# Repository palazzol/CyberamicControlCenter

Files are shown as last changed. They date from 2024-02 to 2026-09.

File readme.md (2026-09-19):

# Unofficial Cyberamic Control Center Archive #

This archive contains unofficial information about the Animatronics Control Computer designed the original Chuck E Cheese's Pizza Time Theatre.  The focus of this archive is to document the historical development and capabilities of this machine.

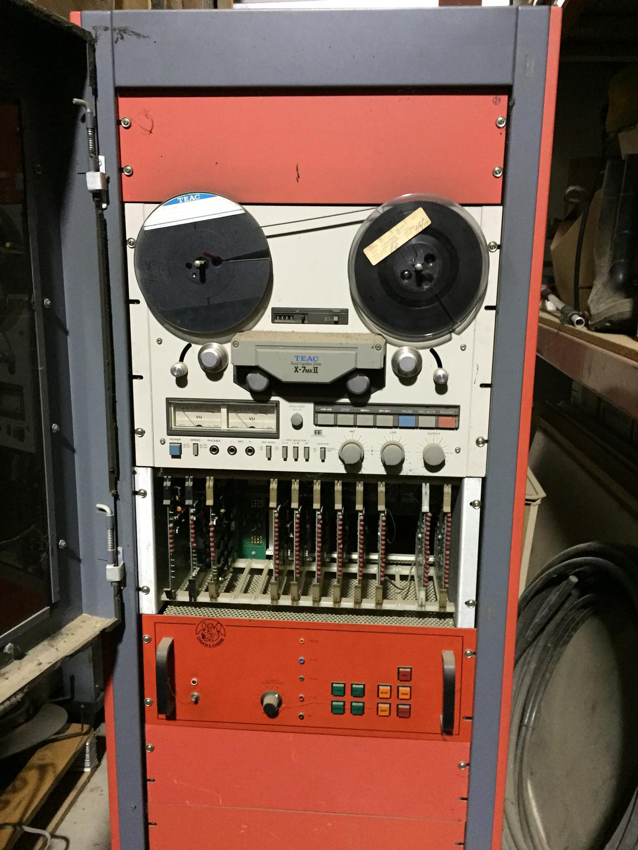
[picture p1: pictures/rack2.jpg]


It was reused in several incarnations over it's lifetime:

## Reel to Reel Configuration: ##
* Based on a 6502 processor and a TEAC Tape Deck, this computer controller the shows such as Dolli Dimples, The Beagles, The King, and the Balcony Stage.

## SVHS Configuration #1: ##
* This same hardware was adapted to play media from SVHS Media.

## SVHS Configuration #2: ##
* Upgraded with a M68HC11 processor, and an external media switcher, this continued to be used to play SVHS media.

## DVD Configuration: ##
* Adapted to DVD Media

If you have any more information or experience with this machine, and would like to help document it's history and behavior, please reach out!

# Latest protocol definitions as decoded from ROM images #
https://docs.google.com/spreadsheets/d/1zTHxSJqbsTTEe6A_9ltzb_rc91lcfIUvdmzVYEThIzg/edit?usp=sharing

# Questions: #

We're working on collecting as much information on how the original Pizza Time Theater system worked and have generated some questions:

* Did the original R2R system use 4-track audio at any stores?

Backplane:
* Was the original card cage a different size to accomodate the 0004 rev.a card?
* Why is the lights 50-pin connector recessed on the card compared to the character card?

Are there more board revisions beyond what we have? looking for:
* Audio board 0003 rev.a, rev.b, and beyond rev.c
* Audio board 0033 rev.b and beyond
* Character board 0004 rev.c and beyond
* Character board 0034 rev.b, rev.f and beyond
* Light board 0021 rev.b to rev.e
* Transport board 0020 rev.a
* Did the original transport card take a external uart clock? per the schematic
* Transport board 0020 rev.c
* CPU board 0001 rev.d and beyond 
* Random movements board?
* Board 0002?

Where are any other rom variants beyond what's in this archive?
* (We strongly believe the original balcony stage rom is not represented here)
* How do the other ROMs handle the buttons on the front panel?

Any more un-scanned documentation?
* Are there any more schematics? 
* Any documentation on how to hook up all the shows?

More show tapes on original media?
* More shows decoded?
* What are the formats for the decoding?
* Is there any metadata they missed like potentially more tracks?

Who else to talk to on this subject?

Extra parts we don't have?

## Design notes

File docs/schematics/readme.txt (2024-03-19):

These are partial, original schematics for the Cyberamic Control System.

The Backplane, Character, and Light Driver schematics seem to be accurate.
However, I do not have a J-19 on my Backplane, nor traces coming from those pins.

I do not have a Solenoid board, or a Transport board, but they seem to be reasonable from the pictures I've seen.

The Audio board schematic is still not found.  I think that board has been accurately replicated in KiCAD. (Evan A. March 19 2024)

The Audio board was the first board to become obsolete, with the Cyberstar upgrade.
Hence information on it is very hard to come by.

-Frank Palazzolo
12 Feb 2024

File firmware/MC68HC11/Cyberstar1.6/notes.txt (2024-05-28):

Memory Map:

0000-03FF Internal RAM
0400-0DFF NVRAM
0E00-0FFF EEPROM
1000-105f Internal Registers

1060-107F ????

1080-1083 Board 1
1084-1087 Board 2
1088-108B Board 3
108C-108F Board 4
1090-1093 Board 5
1094-1097 Board 6
1098-109B Board 7
109C-109F Board 8
10A0-10A3 Board 9
10A4-10A7 Board 10
10A8-10AB Board 11
10AC-10AF Board 12
10B0-10B3 Board 13

10B4-1800 ????

1804-1807 PIASEL
180C-180F SCCSEL

1810-1FFF ????

2000-7FFF NVRAM
8000-FFFF Program ROM

Main PIA pins:

PA0 - ENTER button, input, active low
PA1 - DOWN button, input, active low
PA2 - UP button, input, active low
PA3 - MSGLED backlight, output, active high
PA4 - Button lights clock, output, rising edge active
PA5 - Diagnostic indicator, output, active low
PA6 - RESET button light, output, active high?
PA7 - Tape deck connector input, active low

PB0-PB7 - local DATA bus, output (DA0-DA7)

CA2 - A/V Connector clock, output, rising edge active
CB2 - Tape Deck Connector clock, output, rising edge active

---

Serial port:

Read routines:
    80EF - Looking for a 'D'
    829C - After Printing credits

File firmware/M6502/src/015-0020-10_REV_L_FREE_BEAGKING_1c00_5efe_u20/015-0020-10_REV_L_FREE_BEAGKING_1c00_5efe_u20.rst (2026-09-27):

                              1 
                              2         .area   region1 (ABS)
                              3 
                              4 ;
                              5 ;       Pizza Time Theatre
                              6 ;       Unknown Program (2)
                              7 ;       Version 015-0020-10_REV_L_FREE_BEAGKING
                              8 ;
                              9 ;       This image was recovered from the last quarter of a 2732 and a 2708
                             10 ;
                     0050    11 TIMER_1MS_A     = 0x0050    ; decremented every 1ms
                     0051    12 TIMER_1MS_B     = 0x0051    ; decremented every 1ms
                     0052    13 TIMER_1MS_C     = 0x0052    ; decremented every 1ms
                     0053    14 TIMER_1MS_R     = 0x0053    ; decremented every 1ms, resets to 100
                     0054    15 TIMER_100MS_A   = 0x0054    ; decremented every 0.1s
                     0055    16 TIMER_100MS_R   = 0x0055    ; decremented every 0.1s, resets to 100
                     0056    17 TIMER_10S       = 0x0056    ; decremented every 10s
                     0057    18 TIMER_TMP1      = 0x0057    ; temp timer storage
                     0058    19 ZEROCROSS_CTR   = 0x0058    ; zero crossing counter
                     0059    20 TRACK_CTR       = 0x0059    ; track counter
                     005A    21 PROG_CTR        = 0x005A    ; number of PROG button presses
                             22 
                     005C    23 TAPE_BYTE       = 0x005C    ; storage for incoming serial byte (& 0x7F)
                     005D    24 SOL_MASK        = 0x005D    ; bitmask for solenoids
                     005E    25 CURR_CHANNEL    = 0x005E    ; current channel serial byte
                     005F    26 TIMER_TMP       = 0x005F    ; temp timer storage
                     0060    27 AGC_LEVEL       = 0x0060    ; agc mic level
                     0061    28 AGC_ACCUM       = 0x0061    ; agc mic level accumulator
                     0062    29 AGC_SAMPLES     = 0x0062    ; agc mic sample counter
                     0063    30 AGC_GAIN        = 0x0063    ; agc calculated gain value
                     0064    31 CURR_PORT       = 0x0064    ; current channel port address
                             32 
                             33         .include "../../include/ptt6502.def"
                              1 
                              2 ;
                              3 ; Peripheral Addresses for PTT 6502 system
                              4 ;
                              5 
                     0000     6 RAM_start                       = 0x0000
                              7 
                              8 ; Board Select 1
                     0080     9 board_1_periph$ddr_reg_a        = 0x0080
                     0081    10 board_1_control_reg_a           = 0x0081
                     0082    11 board_1_periph$ddr_reg_b        = 0x0082
                     0083    12 board_1_control_reg_b           = 0x0083
                             13 
                             14 ; Board Select 2
                     0084    15 board_2_periph$ddr_reg_a        = 0x0084
                     0086    16 board_2_periph$ddr_reg_b        = 0x0086
                             17 
                             18 ; Board Select 3
                     0088    19 board_3_periph$ddr_reg_a        = 0x0088
                     008A    20 board_3_periph$ddr_reg_b        = 0x008A
                             21 
                             22 ; Board Select 4
                     008C    23 board_4_periph$ddr_reg_a        = 0x008C
                     008E    24 board_4_periph$ddr_reg_b        = 0x008E
                             25 
                             26 ; Board Select 5
                     0090    27 board_5_periph$ddr_reg_a        = 0x0090
                     0092    28 board_5_periph$ddr_reg_b        = 0x0092
                             29 
                             30 ; Board Select 6
                     0094    31 board_6_periph$ddr_reg_a        = 0x0094
                             32 
                             33 ; Board Select 7
                     0098    34 board_7_periph$ddr_reg_a        = 0x0098
                     009A    35 board_7_periph$ddr_reg_b        = 0x009A
                             36 
                             37 ; Board Select 8
                     009C    38 board_8_periph$ddr_reg_a        = 0x009C
                     009E    39 board_8_periph$ddr_reg_b        = 0x009E
                             40 
                             41 ; UART / Board Select 11
                     0101    42 UART_01                         = 0x0101
                     0102    43 UART_02                         = 0x0102
                             44 
                             45 ; 1st 6532 on CPU board
                     0200    46 U18_PORTA                       = 0x0200
                     0201    47 U18_DDRA                        = 0x0201
                     0202    48 U18_PORTB                       = 0x0202
                     0203    49 U18_DDRB                        = 0x0203
                     0204    50 U18_timer                       = 0x0204
                     0205    51 U18_edge_detect_control_DI_pos  = 0x0205
                     0206    52 U18_06                          = 0x0206    
                     0215    53 U18_timer_8T_DI                 = 0x0215
                     0217    54 U18_17                          = 0x0217
                     021C    55 U18_1C                          = 0x021C    ; timer div by 1, enable interrupt
                     021D    56 U18_1D                          = 0x021D    ; timer div by 1, disable interrupt
                             57 
                             58 ; 2nd 6532 on CPU board
                     0280    59 U19_PORTA                       = 0x0280
                     0281    60 U19_DDRA                        = 0x0281
                     0282    61 U19_PORTB                       = 0x0282
                     0283    62 U19_DDRB                        = 0x0283
                     0285    63 U19_edge_detect_control_DI_pos  = 0x0285
                     0286    64 U19_06                          = 0x0286
                             65 
                             66 ; XPRT / Board Select 12
                     0300    67 transport_periph$ddr_reg_a      = 0x0300
                     0301    68 transport_control_reg_a         = 0x0301
                     0302    69 transport_periph$ddr_reg_b      = 0x0302
                     0303    70 transport_control_reg_b         = 0x0303
                             71 
                             72 ; AUDIO / Board Select 13
                     0380    73 audio_periph$ddr_reg_a          = 0x0380
                     0381    74 audio_control_reg_a             = 0x0381
                     0382    75 audio_periph$ddr_reg_b          = 0x0382
                     0383    76 audio_control_reg_b             = 0x0383
                             77 
                             78 ; Tape Commands
                     0010    79 TAPEMODE_STOP                   = 0x10
                     0020    80 TAPEMODE_FFWD                   = 0x20
                     0040    81 TAPEMODE_REWIND                 = 0x40
                     0080    82 TAPEMODE_PLAY                   = 0x80
                             83 
                             84 
                             85 
                             86 
                             87 
                             88 
                             34 
   1C00                      35         .org    0x1C00
                             36 ;
   1C00                      37 RESET:
   1C00 D8            [ 2]   38         cld                                             ; No decimal mode
   1C01 78            [ 2]   39         sei                                             ; Interrupts are not used
   1C02 A2 F0         [ 2]   40         ldx     #0xF0                                   ; Stack is at 0x01F0
   1C04 9A            [ 2]   41         txs
   1C05 A9 00         [ 2]   42         lda     #0x00                                   ; Clear RAM
   1C07 A2 10         [ 2]   43         ldx     #0x10                                   ; from 0x0010 to 0x007F
   1C09                      44 ZERORAM:
   1C09 95 00         [ 4]   45         sta     RAM_start,x
   1C0B E8            [ 2]   46         inx
   1C0C E0 80         [ 2]   47         cpx     #0x80
   1C0E D0 F9         [ 4]   48         bne     ZERORAM
   1C10 A9 00         [ 2]   49         lda     #0x00                                   ; Initialize these registers to 0x00
   1C12 8D 01 03      [ 4]   50         sta     transport_control_reg_a                 ; Clear transport control A, select DDRA
   1C15 8D 00 03      [ 4]   51         sta     transport_periph$ddr_reg_a              ; UART data inputs
   1C18 8D 81 03      [ 4]   52         sta     audio_control_reg_a                     ; Clear audio control A, select DDRA
   1C1B 8D 80 03      [ 4]   53         sta     audio_periph$ddr_reg_a                  ; Comparator inputs
   1C1E 8D 83 03      [ 4]   54         sta     audio_control_reg_b                     ; Clear audio control B
   1C21 8D 05 02      [ 4]   55         sta     U18_edge_detect_control_DI_pos          ; Detect PROG button release
   1C24 8D 03 03      [ 4]   56         sta     transport_control_reg_b                 ; Clear transport control B, select DDRB
   1C27 8D 01 02      [ 4]   57         sta     U18_DDRA                                ; Buttons are inputs
   1C2A A9 02         [ 2]   58         lda     #0x02
   1C2C 8D 81 02      [ 4]   59         sta     U19_DDRA                                ; AGC and MIKESW are inputs, RESET Light output
   1C2F A9 FF         [ 2]   60         lda     #0xFF
   1C31 8D 82 03      [ 4]   61         sta     audio_periph$ddr_reg_b                  ; DAC08 outputs
   1C34 8D 03 02      [ 4]   62         sta     U18_DDRB                                ; Button lights are outputs
   1C37 8D 83 02      [ 4]   63         sta     U19_DDRB                                ; CPU card lights are outputs
   1C3A A9 FC         [ 2]   64         lda     #0xFC
   1C3C 8D 02 03      [ 4]   65         sta     transport_periph$ddr_reg_b              ; transport control, chip control are outputs, PB1 & PB0 inputs
   1C3F A9 2E         [ 2]   66         lda     #0x2E
   1C41 8D 01 03      [ 4]   67         sta     transport_control_reg_a                 ; transport CA2 is Read strobe (~DDR), set IRQA bit on ~DR low to high 
   1C44 8D 03 03      [ 4]   68         sta     transport_control_reg_b                 ; transport CB2 is Write strobe (~THRL), set IRQB bit on CB1 low to high
   1C47 A9 3C         [ 2]   69         lda     #0x3C
   1C49 8D 81 03      [ 4]   70         sta     audio_control_reg_a                     ; CA2 High - Disable BG Audio
   1C4C 8D 83 03      [ 4]   71         sta     audio_control_reg_b                     ; CB2 high - Disable Tape Audio
   1C4F A9 64         [ 2]   72         lda     #0x64
   1C51 85 53         [ 3]   73         sta     TIMER_1MS_R                             ; 100 - init 1 msec master counter
   1C53 A9 1E         [ 2]   74         lda     #0x1E
   1C55 85 56         [ 3]   75         sta     TIMER_10S                               ; Init a 5 minute timer
   1C57 A9 64         [ 2]   76         lda     #0x64
   1C59 85 55         [ 3]   77         sta     TIMER_100MS_R                           ; 100 - init 0.1 sec master counter
   1C5B A9 10         [ 2]   78         lda     #0x10                                   ; 16
   1C5D 85 63         [ 3]   79         sta     AGC_GAIN                                ; Set initial AGC gain value
   1C5F A9 10         [ 2]   80         lda     #TAPEMODE_STOP
   1C61 20 7C 1D      [ 6]   81         jsr     TAPECMD                                 ; STOP tape
   1C64 A9 28         [ 2]   82         lda     #0x28                                   ; this will count 4 seconds
   1C66 85 54         [ 3]   83         sta     TIMER_100MS_A
   1C68 A9 64         [ 2]   84         lda     #0x64                                   ; reset master timer
   1C6A 85 53         [ 3]   85         sta     TIMER_1MS_R
   1C6C                      86 $1:
   1C6C 20 8D 1E      [ 6]   87         jsr     TUPDATE                                 ; do not much for 4 seconds
   1C6F A5 54         [ 3]   88         lda     TIMER_100MS_A
   1C71 D0 F9         [ 4]   89         bne     $1
   1C73                      90 REWIND:
   1C73 A9 40         [ 2]   91         lda     #TAPEMODE_REWIND
   1C75 20 7C 1D      [ 6]   92         jsr     TAPECMD                                 ; REWIND tape
   1C78                      93 $22:
   1C78 A9 00         [ 2]   94         lda     #0x00
   1C7A 85 58         [ 3]   95         sta     ZEROCROSS_CTR                           ; counter to zero
                             96 ; Look for the long tone at the beginning of tape
   1C7C                      97 $2:
   1C7C 20 8D 1E      [ 6]   98         jsr     TUPDATE                                 ; housekeeping
   1C7F AD 03 03      [ 4]   99         lda     transport_control_reg_b                 ; loop until we see tone marking beginning of tape
   1C82 10 F8         [ 4]  100         bpl     $2
   1C84 A9 06         [ 2]  101         lda     #0x06
   1C86 85 54         [ 3]  102         sta     TIMER_100MS_A                           ; set 0.6 second timer
   1C88 A9 64         [ 2]  103         lda     #0x64                                   ; 100 rising edge transitions
   1C8A 85 53         [ 3]  104         sta     TIMER_1MS_R
   1C8C                     105 $3:
   1C8C 20 8D 1E      [ 6]  106         jsr     TUPDATE                                 ; housekeeping
   1C8F AD 03 03      [ 4]  107         lda     transport_control_reg_b                 ; loop until 100 transport CB1 rising edges or 0.6 secs expired
   1C92 10 0B         [ 4]  108         bpl     $4                                      ; (> 83.333 Hz for 100 zero crossings)
   1C94 E6 58         [ 5]  109         inc     ZEROCROSS_CTR                           ; count transitions
   1C96 AD 02 03      [ 4]  110         lda     transport_periph$ddr_reg_b
   1C99 A5 58         [ 3]  111         lda     ZEROCROSS_CTR
   1C9B C9 64         [ 2]  112         cmp     #0x64
   1C9D B0 0B         [ 4]  113         bcs     FINDTRK                                 ; happened 100 times, tape is at the beginning, jump ahead
   1C9F                     114 $4:
   1C9F A5 54         [ 3]  115         lda     TIMER_100MS_A
   1CA1 D0 E9         [ 4]  116         bne     $3
   1CA3 4C 78 1C      [ 3]  117         jmp     $22
                            118 ; unused instructions start
   1CA6 C9 60         [ 2]  119         cmp     #0x60
   1CA8 90 00         [ 4]  120         bcc     FINDTRK
                            121 ; unused instructions end
                            122 ;
   1CAA                     123 FINDTRK:
   1CAA A9 20         [ 2]  124         lda     #TAPEMODE_FFWD
   1CAC 20 7C 1D      [ 6]  125         jsr     TAPECMD                                 ; FFWD tape
   1CAF A9 19         [ 2]  126         lda     #0x19
   1CB1 85 54         [ 3]  127         sta     TIMER_100MS_A                           ; 2.5 secs
   1CB3 A9 64         [ 2]  128         lda     #0x64
   1CB5 85 53         [ 3]  129         sta     TIMER_1MS_R
   1CB7                     130 $5:
   1CB7 20 8D 1E      [ 6]  131         jsr     TUPDATE                                 ; do housekeeping stuff
   1CBA A5 54         [ 3]  132         lda     TIMER_100MS_A
   1CBC D0 F9         [ 4]  133         bne     $5
   1CBE A9 00         [ 2]  134         lda     #0x00
   1CC0 85 59         [ 3]  135         sta     TRACK_CTR
   1CC2 20 97 1D      [ 6]  136         jsr     WAITTONE                                ; wait for tone signaling beginning of track
   1CC5 A9 40         [ 2]  137         lda     #TAPEMODE_REWIND
   1CC7 20 7C 1D      [ 6]  138         jsr     TAPECMD                                 ; REWIND tape
   1CCA 20 97 1D      [ 6]  139         jsr     WAITTONE                                ; wait for tone signaling beginning of track
   1CCD A9 FA         [ 2]  140         lda     #0xFA
   1CCF 85 50         [ 3]  141         sta     TIMER_1MS_A
   1CD1                     142 $30:
   1CD1 20 8D 1E      [ 6]  143         jsr     TUPDATE                                 ; housekeeping
   1CD4 A5 50         [ 3]  144         lda     TIMER_1MS_A
   1CD6 D0 F9         [ 4]  145         bne     $30                                     ; delay for 250 ms
   1CD8 A9 20         [ 2]  146         lda     #TAPEMODE_FFWD
   1CDA 20 7C 1D      [ 6]  147         jsr     TAPECMD                                 ; FFWD tape
   1CDD 20 97 1D      [ 6]  148         jsr     WAITTONE                                ; wait for tone signaling beginning of track
   1CE0 E6 59         [ 5]  149         inc     TRACK_CTR
   1CE2 A9 10         [ 2]  150         lda     #TAPEMODE_STOP
   1CE4 20 7C 1D      [ 6]  151         jsr     TAPECMD                                 ; STOP tape
   1CE7 A9 80         [ 2]  152         lda     #TAPEMODE_PLAY
   1CE9 20 7C 1D      [ 6]  153         jsr     TAPECMD                                 ; PLAY tape
   1CEC 20 BA 1D      [ 6]  154         jsr     WAITCD                                  ; wait for carrier
   1CEF A9 10         [ 2]  155         lda     #TAPEMODE_STOP
   1CF1 20 7C 1D      [ 6]  156         jsr     TAPECMD                                 ; STOP Tape
   1CF4 20 4F 1D      [ 6]  157         jsr     INITBRDS                                ; init the boards
   1CF7                     158 WAITPLAY:
   1CF7 20 8D 1E      [ 6]  159         jsr     TUPDATE                                 ; do housekeeping stuff
   1CFA 20 1A 1F      [ 6]  160         jsr     AGCUPD                                  ; do AGC Mic Logic
   1CFD A5 5A         [ 3]  161         lda     PROG_CTR                                ; wait until we are triggered
   1CFF D0 10         [ 4]  162         bne     STARTPLAY                               ; then jump
   1D01 A9 02         [ 2]  163         lda     #0x02                                   ; else
   1D03 8D 80 02      [ 4]  164         sta     U19_PORTA                               ; turn on RESET button light
   1D06 A9 00         [ 2]  165         lda     #0x00
   1D08 8D 02 02      [ 4]  166         sta     U18_PORTB                               ; turn on all other button lights
   1D0B A5 56         [ 3]  167         lda     TIMER_10S                               ; has the 8 minute timer run out?
   1D0D D0 E8         [ 4]  168         bne     WAITPLAY                                ; no, keep looping
   1D0F E6 5A         [ 5]  169         inc     PROG_CTR                                ; yes, simulate a PROG button press
                            170 ;   we have been started!
   1D11                     171 STARTPLAY:
   1D11 20 4F 1D      [ 6]  172         jsr     INITBRDS                                ; init the boards
   1D14 A9 00         [ 2]  173         lda     #0x00
   1D16 8D 80 02      [ 4]  174         sta     U19_PORTA                               ; turn off RESET button light
   1D19 A9 80         [ 2]  175         lda     #0x80
   1D1B 8D 02 02      [ 4]  176         sta     U18_PORTB                               ; turn off all but PROG light
   1D1E A9 80         [ 2]  177         lda     #TAPEMODE_PLAY
   1D20 20 7C 1D      [ 6]  178         jsr     TAPECMD                                 ; PLAY tape
   1D23 20 BA 1D      [ 6]  179         jsr     WAITCD                                  ; wait for carrier
   1D26 C6 5A         [ 5]  180         dec     PROG_CTR                                  ; no longer triggered
   1D28 20 E0 1D      [ 6]  181         jsr     PLAYTRK                                 ; play a track!
   1D2B 20 4F 1D      [ 6]  182         jsr     INITBRDS                                ; init the boards
   1D2E A9 1E         [ 2]  183         lda     #0x1E
   1D30 85 56         [ 3]  184         sta     TIMER_10S                               ; set a 5 min timer
   1D32 A9 64         [ 2]  185         lda     #0x64
   1D34 85 55         [ 3]  186         sta     TIMER_100MS_R
   1D36 E6 59         [ 5]  187         inc     TRACK_CTR                               ; track counter
   1D38 A5 59         [ 3]  188         lda     TRACK_CTR
   1D3A C9 1A         [ 2]  189         cmp     #0x1A                                   ; 26?
   1D3C 90 03         [ 4]  190         bcc     NEXTTRK
   1D3E 4C 73 1C      [ 3]  191         jmp     REWIND                                  ; rewind the tape after the total number of tracks are done
                            192 ; go to next track
   1D41                     193 NEXTTRK:
   1D41 20 BA 1D      [ 6]  194         jsr     WAITCD                                  ; wait for carrier
   1D44 A9 10         [ 2]  195         lda     #TAPEMODE_STOP
   1D46 20 7C 1D      [ 6]  196         jsr     TAPECMD                                 ; STOP tape
   1D49 20 D1 1E      [ 6]  197         jsr     AGCMICRD                                ; Read the AGC mic level
   1D4C 4C F7 1C      [ 3]  198         jmp     WAITPLAY
                            199 ;
                            200 ;       Init boards
                            201 ;
   1D4F                     202 INITBRDS:
   1D4F A9 3C         [ 2]  203         lda     #0x3C
   1D51 8D 83 03      [ 4]  204         sta     audio_control_reg_b                     ; CB2 High (Disable Tape Audio)
   1D54 A9 34         [ 2]  205         lda     #0x34
   1D56 8D 81 03      [ 4]  206         sta     audio_control_reg_a                     ; CA2 Low (Enable BG Audio)
   1D59 A2 00         [ 2]  207         ldx     #0x00
   1D5B                     208 NEXTBRD:
   1D5B A9 30         [ 2]  209         lda     #0x30
   1D5D 95 81         [ 4]  210         sta     board_1_control_reg_a,x                 ; boardX CA2 low, DDR select
   1D5F 95 83         [ 4]  211         sta     board_1_control_reg_b,x                 ; boardX CB2 low, DDR select
   1D61 A9 FF         [ 2]  212         lda     #0xFF
   1D63 95 80         [ 4]  213         sta     board_1_periph$ddr_reg_a,x              ; all A pins to outputs
   1D65 95 82         [ 4]  214         sta     board_1_periph$ddr_reg_b,x              ; all B pins to outputs
   1D67 A9 34         [ 2]  215         lda     #0x34
   1D69 95 81         [ 4]  216         sta     board_1_control_reg_a,x                 ; A peripheral selected
   1D6B 95 83         [ 4]  217         sta     board_1_control_reg_b,x                 ; B peripheral selected
   1D6D A9 00         [ 2]  218         lda     #0x00
   1D6F 95 80         [ 4]  219         sta     board_1_periph$ddr_reg_a,x              ; A solenoids off
   1D71 95 82         [ 4]  220         sta     board_1_periph$ddr_reg_b,x              ; B solenoids off
   1D73 E8            [ 2]  221         inx
   1D74 E8            [ 2]  222         inx
   1D75 E8            [ 2]  223         inx
   1D76 E8            [ 2]  224         inx
   1D77 E0 20         [ 2]  225         cpx     #0x20                                   ; do for boards 1-8
   1D79 90 E0         [ 4]  226         bcc     NEXTBRD
   1D7B 60            [ 6]  227         rts
                            228 ;
                            229 ;       Send Transport command for 0.250 sec
                            230 ;       (Unified)
                            231 ;
   1D7C                     232 TAPECMD:
   1D7C 8D 02 03      [ 4]  233         sta     transport_periph$ddr_reg_b              ; enable output line
   1D7F A9 FA         [ 2]  234         lda     #0xFA
   1D81 85 50         [ 3]  235         sta     TIMER_1MS_A
   1D83                     236 $6:
   1D83 20 8D 1E      [ 6]  237         jsr     TUPDATE                                 ; check for PROG button push
   1D86 A5 50         [ 3]  238         lda     TIMER_1MS_A
   1D88 D0 F9         [ 4]  239         bne     $6
   1D8A AD 02 03      [ 4]  240         lda     transport_periph$ddr_reg_b
   1D8D 29 60         [ 2]  241         and     #TAPEMODE_REWIND | #TAPEMODE_FFWD       ; Is it a REWIND or FFWD?
   1D8F D0 05         [ 4]  242         bne     $31                                     ; Yes, go to exit
   1D91 A9 00         [ 2]  243         lda     #0x00                                   ; else unassert STOP or PLAY
   1D93 8D 02 03      [ 4]  244         sta     transport_periph$ddr_reg_b              ; and then exit
   1D96                     245 $31:
   1D96 60            [ 6]  246         rts
                            247 ;
                            248 ;       Wait for tone during Fast Forward, signaling beginning of track
                            249 ;       (50Hz or above, for 33 zero crossing) 
                            250 ;
   1D97                     251 WAITTONE:
   1D97 A9 00         [ 2]  252         lda     #0x00
   1D99 85 58         [ 3]  253         sta     ZEROCROSS_CTR
   1D9B                     254 $8:
   1D9B AD 02 03      [ 4]  255         lda     transport_periph$ddr_reg_b
   1D9E A9 0A         [ 2]  256         lda     #0x0A
   1DA0 85 50         [ 3]  257         sta     TIMER_1MS_A                             ; 10 msec
   1DA2 E6 58         [ 5]  258         inc     ZEROCROSS_CTR
   1DA4 A5 58         [ 3]  259         lda     ZEROCROSS_CTR
   1DA6 C9 21         [ 2]  260         cmp     #0x21                                   ; wait for 33 rising edges, each within 10ms window
   1DA8 B0 0F         [ 4]  261         bcs     $10                                     ; timeout - exit
   1DAA                     262 $9:
   1DAA 20 8D 1E      [ 6]  263         jsr     TUPDATE                                 ; housekeeping
   1DAD A5 50         [ 3]  264         lda     TIMER_1MS_A
   1DAF F0 E6         [ 4]  265         beq     WAITTONE                                ; 10 msec done yet? then loop
   1DB1 AD 03 03      [ 4]  266         lda     transport_control_reg_b                 ; transport CB1 rising edge?
   1DB4 10 F4         [ 4]  267         bpl     $9                                      ; if not, extend the looping
   1DB6 4C 9B 1D      [ 3]  268         jmp     $8                                      ; else loop but keep timeout going
   1DB9                     269 $10:
   1DB9 60            [ 6]  270         rts
                            271 ;
                            272 ;       Wait for carrier / start of data
                            273 ;
                            274 
                            275 ; Wait for 250ms
   1DBA                     276 WAITCD:
   1DBA A9 FA         [ 2]  277         lda     #0xFA
   1DBC 85 50         [ 3]  278         sta     TIMER_1MS_A                             ; 250 msec
   1DBE                     279 $11:
   1DBE 20 8D 1E      [ 6]  280         jsr     TUPDATE                                 ; housekeeping
   1DC1 A5 50         [ 3]  281         lda     TIMER_1MS_A
   1DC3 D0 F9         [ 4]  282         bne     $11
                            283 
                            284 ; Wait for 160ms of consecutive zero crossings
   1DC5                     285 $12:
   1DC5 20 8D 1E      [ 6]  286         jsr     TUPDATE                                 ; housekeeping
   1DC8 AD 02 03      [ 4]  287         lda     transport_periph$ddr_reg_b
   1DCB 6A            [ 2]  288         ror     a
   1DCC 90 F7         [ 4]  289         bcc     $12
   1DCE A9 A0         [ 2]  290         lda     #0xA0                                   ; 160 msec
   1DD0 85 50         [ 3]  291         sta     TIMER_1MS_A
   1DD2                     292 $13:
   1DD2 20 8D 1E      [ 6]  293         jsr     TUPDATE                                 ; housekeeping
   1DD5 AD 02 03      [ 4]  294         lda     transport_periph$ddr_reg_b
   1DD8 6A            [ 2]  295         ror     a
   1DD9 90 EA         [ 4]  296         bcc     $12
   1DDB A5 50         [ 3]  297         lda     TIMER_1MS_A
   1DDD D0 F3         [ 4]  298         bne     $13
   1DDF 60            [ 6]  299         rts
                            300 ;
                            301 ;       Play a track
                            302 ;
   1DE0                     303 PLAYTRK:
   1DE0 AD 00 03      [ 4]  304         lda     transport_periph$ddr_reg_a
   1DE3 A9 40         [ 2]  305         lda     #0x40
   1DE5 85 82         [ 3]  306         sta     board_1_periph$ddr_reg_b                ; only Board 1 PB6 on
   1DE7 85 86         [ 3]  307         sta     board_2_periph$ddr_reg_b                ; only Board 2 PB6 on
   1DE9 85 8A         [ 3]  308         sta     board_3_periph$ddr_reg_b                ; only Board 3 PB6 on
   1DEB 85 8E         [ 3]  309         sta     board_4_periph$ddr_reg_b                ; only Board 4 PB6 on
   1DED A9 3C         [ 2]  310         lda     #0x3C
   1DEF 8D 81 03      [ 4]  311         sta     audio_control_reg_a                     ; CA2 High (Disable Other Audio)
   1DF2 A9 34         [ 2]  312         lda     #0x34
   1DF4 8D 83 03      [ 4]  313         sta     audio_control_reg_b                     ; CB2 Low (Enable Tape Audio)
   1DF7 A9 60         [ 2]  314         lda     #0x60
   1DF9 85 82         [ 3]  315         sta     board_1_periph$ddr_reg_b                ; ???
   1DFB                     316 $14:
   1DFB AD 02 03      [ 4]  317         lda     transport_periph$ddr_reg_b
   1DFE 4A            [ 2]  318         lsr     a
   1DFF 90 11         [ 4]  319         bcc     LOSTCD                                  ; b0=0, no carrier, exit
   1E01 20 1A 1F      [ 6]  320         jsr     AGCUPD                                  ; do AGC Mic Logic
   1E04 20 8D 1E      [ 6]  321         jsr     TUPDATE                                 ; housekeeping
   1E07 AD 01 03      [ 4]  322         lda     transport_control_reg_a                 ; Did we get a byte?
   1E0A 10 EF         [ 4]  323         bpl     $14                                     ; No, loop
   1E0C 20 24 1E      [ 6]  324         jsr     PROTOHAND                               ; Yes, Process Incoming Byte
   1E0F 4C FB 1D      [ 3]  325         jmp     $14
                            326 
                            327 ;       Lost carrier - wait 100 msec for more data before giving up
   1E12                     328 LOSTCD:
   1E12 A9 64         [ 2]  329         lda     #0x64                                   ; 100 msec
   1E14 85 50         [ 3]  330         sta     TIMER_1MS_A
   1E16                     331 $15:
   1E16 20 8D 1E      [ 6]  332         jsr     TUPDATE
   1E19 AD 02 03      [ 4]  333         lda     transport_periph$ddr_reg_b
   1E1C 4A            [ 2]  334         lsr     a
   1E1D B0 C1         [ 4]  335         bcs     PLAYTRK                                 ; carrier
   1E1F A5 50         [ 3]  336         lda     TIMER_1MS_A
   1E21 D0 F3         [ 4]  337         bne     $15
   1E23 60            [ 6]  338         rts
                            339 ;
                            340 ; Protocol handler
                            341 ;
   1E24                     342 PROTOHAND:
   1E24 AD 00 03      [ 4]  343         lda     transport_periph$ddr_reg_a
   1E27 29 7F         [ 2]  344         and     #0x7F                                   ; insure data is ASCII
   1E29 85 5C         [ 3]  345         sta     TAPE_BYTE                               ; store it here
   1E2B 29 7E         [ 2]  346         and     #0x7E                                   ; ignore bottom bit
   1E2D C9 22         [ 2]  347         cmp     #0x22                                   ; is it 0x22 or 0x23?
   1E2F F0 3A         [ 4]  348         beq     PROCCHNL                                ; if so, process as channel
   1E31 C9 32         [ 2]  349         cmp     #0x32                                   ; is it < 0x32 ?
   1E33 90 4F         [ 4]  350         bcc     $18                                     ; ignore it
   1E35 C9 3A         [ 2]  351         cmp     #0x3A                                   ; is it < 0x3A
   1E37 90 32         [ 4]  352         bcc     PROCCHNL                                ; process as channel (0x32 to 0x39)
   1E39 A5 5C         [ 3]  353         lda     TAPE_BYTE
   1E3B C9 41         [ 2]  354         cmp     #0x41                                   ; is it < 0x41?
   1E3D 90 45         [ 4]  355         bcc     $18                                     ; ignore it
   1E3F C9 51         [ 2]  356         cmp     #0x51                                   ; is it >= 0x51?
   1E41 B0 41         [ 4]  357         bcs     $18                                     ; ignore it
   1E43 A6 64         [ 3]  358         ldx     CURR_PORT                               ; X = current board address
   1E45 38            [ 2]  359         sec                                             ; (it's 0x41 to 0x50)
   1E46 E9 41         [ 2]  360         sbc     #0x41                                   ; subtract 0x41
   1E48 C9 08         [ 2]  361         cmp     #0x08
   1E4A 90 02         [ 4]  362         bcc     $16                                     ; process as command
   1E4C E8            [ 2]  363         inx
   1E4D E8            [ 2]  364         inx
   1E4E                     365 $16:
   1E4E 29 07         [ 2]  366         and     #0x07                                   ; lookup bitmask in A
   1E50 A8            [ 2]  367         tay
   1E51 B9 85 1E      [ 5]  368         lda     MASKTBL,y
   1E54 85 5D         [ 3]  369         sta     SOL_MASK                                ; store mask in SOL_MASK
   1E56 A5 5E         [ 3]  370         lda     CURR_CHANNEL
   1E58 4A            [ 2]  371         lsr     a                                       ; get on/off in carry
   1E59 B0 09         [ 4]  372         bcs     $17                                     ; if on, jump
   1E5B A5 5D         [ 3]  373         lda     SOL_MASK
   1E5D 49 FF         [ 2]  374         eor     #0xFF
   1E5F 35 00         [ 4]  375         and     RAM_start,x
   1E61 95 00         [ 4]  376         sta     RAM_start,x                             ; turn off solenoid
   1E63 60            [ 6]  377         rts
                            378 ;
   1E64                     379 $17:
   1E64 A5 5D         [ 3]  380         lda     SOL_MASK
   1E66 15 00         [ 4]  381         ora     RAM_start,x
   1E68 95 00         [ 4]  382         sta     RAM_start,x                             ; turn on solenoid
   1E6A 60            [ 6]  383         rts
                            384 ;
   1E6B                     385 PROCCHNL:
   1E6B A5 5C         [ 3]  386         lda     TAPE_BYTE                               ; put channel byte in CURR_CHANNEL
   1E6D 85 5E         [ 3]  387         sta     CURR_CHANNEL
   1E6F 29 7E         [ 2]  388         and     #0x7E
   1E71 C9 22         [ 2]  389         cmp     #0x22
   1E73 D0 05         [ 4]  390         bne     CONVCHNL
   1E75 A9 98         [ 2]  391         lda     #0x98                                   ; process 0x22 or 0x23
   1E77 85 64         [ 3]  392         sta     CURR_PORT                               ; set this to 0x98 - board 7
   1E79 60            [ 6]  393         rts
                            394 ;
   1E7A                     395 CONVCHNL:
   1E7A 38            [ 2]  396         sec                                             ; process channel
   1E7B E9 32         [ 2]  397         sbc     #0x32
   1E7D 0A            [ 2]  398         asl     a
   1E7E 18            [ 2]  399         clc
   1E7F 69 80         [ 2]  400         adc     #0x80
   1E81 85 64         [ 3]  401         sta     CURR_PORT                               ; (X-0x32) * 2 + 0x80
   1E83 60            [ 6]  402         rts
   1E84                     403 $18:
   1E84 60            [ 6]  404         rts
                            405 ;
                            406 ; bit mask table
                            407 ;
   1E85                     408 MASKTBL:
   1E85 01 02 04 08         409         .db     0x01,0x02,0x04,0x08
   1E89 10 20 40 80         410         .db     0x10,0x20,0x40,0x80
                            411 ;
                            412 ;       Housekeeping routine
                            413 ;       TIMER_1MS_A used on entry
                            414 ;
   1E8D                     415 TUPDATE:
   1E8D AD 05 02      [ 4]  416         lda     U18_edge_detect_control_DI_pos          ; Did the PROG button get pushed or timer expire?
   1E90 85 5F         [ 3]  417         sta     TIMER_TMP                               ; store this state in 5F
   1E92 F0 3C         [ 4]  418         beq     TEXIT                                   ; No flags set, return
   1E94 29 40         [ 2]  419         and     #0x40                                   ; PROG pushed?
   1E96 F0 04         [ 4]  420         beq     $20                                     ; if not, check if timer expired
   1E98 A9 01         [ 2]  421         lda     #0x01
   1E9A 85 5A         [ 3]  422         sta     PROG_CTR                                ; Mark as started
   1E9C                     423 $20:
   1E9C A5 5F         [ 3]  424         lda     TIMER_TMP                               ; check timer irq bit
   1E9E 10 30         [ 4]  425         bpl     TEXIT                                   ; if timer not expired, return
                            426 ; Adjust Timer routine
   1EA0 AD 04 02      [ 4]  427         lda     U18_timer                               ; read timer in U18
   1EA3 49 FF         [ 2]  428         eor     #0xFF                                   ; flip the bits
   1EA5 4A            [ 2]  429         lsr     a                                       ; keep the top 5 bits
   1EA6 4A            [ 2]  430         lsr     a
   1EA7 4A            [ 2]  431         lsr     a
   1EA8 85 57         [ 3]  432         sta     TIMER_TMP1                              ; store them
   1EAA 90 02         [ 4]  433         bcc     $21                                     ; bcc on timer bit D2
   1EAC E6 57         [ 5]  434         inc     TIMER_TMP1                              ; round up?
                            435                                                         ; now TIMER_TMP1 has the number of 8us 
                            436                                                         ;   intervals since timer expired
   1EAE                     437 $21:
   1EAE A9 7A         [ 2]  438         lda     #0x7A                                   ; reset timer to expire every 0x7A*8 ~= 976 usec?
   1EB0 38            [ 2]  439         sec                                             ; with programming delays, this is 1 msec
   1EB1 E5 57         [ 3]  440         sbc     TIMER_TMP1
   1EB3 8D 15 02      [ 4]  441         sta     U18_timer_8T_DI                         ; set timer
   1EB6 C6 50         [ 5]  442         dec     TIMER_1MS_A                             ; decrement these timers every timer reset (1ms)
   1EB8 C6 51         [ 5]  443         dec     TIMER_1MS_B
   1EBA C6 52         [ 5]  444         dec     TIMER_1MS_C
   1EBC C6 53         [ 5]  445         dec     TIMER_1MS_R
   1EBE D0 10         [ 4]  446         bne     TEXIT                                   ; if timer TIMER_1MS_R expires, then wrap to 100
   1EC0 A9 64         [ 2]  447         lda     #0x64                                   ; 100
   1EC2 85 53         [ 3]  448         sta     TIMER_1MS_R
   1EC4 C6 54         [ 5]  449         dec     TIMER_100MS_A
   1EC6 C6 55         [ 5]  450         dec     TIMER_100MS_R
   1EC8 D0 06         [ 4]  451         bne     TEXIT                                   ; if timer TIMER_100MS_R expires, then wrap to 100
   1ECA A9 64         [ 2]  452         lda     #0x64                                   ; reset to 10 seconds?
   1ECC 85 55         [ 3]  453         sta     TIMER_100MS_R
   1ECE C6 56         [ 5]  454         dec     TIMER_10S
   1ED0                     455 TEXIT:
   1ED0 60            [ 6]  456         rts
                            457 ;
                            458 ;       Read the AGC mic level
                            459 ;       Take the average of 8 samples, and put it into AGC_LEVEL (range is 0 to 8)
                            460 ;
   1ED1                     461 AGCMICRD:
   1ED1 A9 00         [ 2]  462         lda     #0x00
   1ED3 85 61         [ 3]  463         sta     AGC_ACCUM                               ; init final agc value
   1ED5 85 62         [ 3]  464         sta     AGC_SAMPLES                             ; init agc sample counter
   1ED7 A9 0A         [ 2]  465         lda     #0x0A
   1ED9 85 54         [ 3]  466         sta     TIMER_100MS_A                           ; Start a 1 second timer
   1EDB A9 64         [ 2]  467         lda     #0x64
   1EDD 85 53         [ 3]  468         sta     TIMER_1MS_R
   1EDF                     469 $23:
   1EDF 20 8D 1E      [ 6]  470         jsr     TUPDATE                                 ; housekeeping
   1EE2 A5 54         [ 3]  471         lda     TIMER_100MS_A
   1EE4 D0 F9         [ 4]  472         bne     $23                                     ; if 1 sec, do housekeeping
   1EE6 A9 0A         [ 2]  473         lda     #0x0A
   1EE8 85 54         [ 3]  474         sta     TIMER_100MS_A
   1EEA A9 64         [ 2]  475         lda     #0x64
   1EEC 85 53         [ 3]  476         sta     TIMER_1MS_R                             ; reset timer
   1EEE A5 62         [ 3]  477         lda     AGC_SAMPLES
   1EF0 C9 08         [ 2]  478         cmp     #0x08                                   ; 8 samples?
   1EF2 F0 15         [ 4]  479         beq     $27                                     ; yes - jump to final calculation
   1EF4 E6 62         [ 5]  480         inc     AGC_SAMPLES                             ; increment the sample counter
   1EF6 A2 09         [ 2]  481         ldx     #0x09
   1EF8 38            [ 2]  482         sec
   1EF9 AD 80 03      [ 4]  483         lda     audio_periph$ddr_reg_a                  ; read the agc mic level
   1EFC                     484 $24:                                                    ; read the most significant high bit
   1EFC 2A            [ 2]  485         rol     a
   1EFD CA            [ 2]  486         dex
   1EFE 90 FC         [ 4]  487         bcc     $24
   1F00 18            [ 2]  488         clc
   1F01 8A            [ 2]  489         txa                                             ; 8=high bit7, 0=no high bits
   1F02 65 61         [ 3]  490         adc     AGC_ACCUM                               ; add it into AGC_ACCUM (do this 8 times)
   1F04 85 61         [ 3]  491         sta     AGC_ACCUM
   1F06 4C DF 1E      [ 3]  492         jmp     $23
                            493 ;
   1F09                     494 $27:
   1F09 46 61         [ 5]  495         lsr     AGC_ACCUM                               ; divide by 8 (average of 8 samples)
   1F0B 46 61         [ 5]  496         lsr     AGC_ACCUM
   1F0D 46 61         [ 5]  497         lsr     AGC_ACCUM
   1F0F A5 61         [ 3]  498         lda     AGC_ACCUM
   1F11 85 60         [ 3]  499         sta     AGC_LEVEL                               ; store agc value in AGC_LEVEL
   1F13 A9 00         [ 2]  500         lda     #0x00
   1F15 85 61         [ 3]  501         sta     AGC_ACCUM                               ; clear these 2 and return
   1F17 85 62         [ 3]  502         sta     AGC_SAMPLES
   1F19 60            [ 6]  503         rts
                            504 ;
                            505 ;        Do AGC Mic Logic
                            506 ;
   1F1A                     507 AGCUPD:
   1F1A AD 80 02      [ 4]  508         lda     U19_PORTA                               ; read AGC knob
   1F1D 49 FF         [ 2]  509         eor     #0xFF                                   ; invert the bits
   1F1F 4A            [ 2]  510         lsr     a                                       ; get into lower nibble
   1F20 4A            [ 2]  511         lsr     a
   1F21 4A            [ 2]  512         lsr     a
   1F22 4A            [ 2]  513         lsr     a
   1F23 18            [ 2]  514         clc
   1F24 65 60         [ 3]  515         adc     AGC_LEVEL                               ; add audio level to it
   1F26 AA            [ 2]  516         tax
   1F27 BD 4D 1F      [ 5]  517         lda     AGCTABLE,x                              ; and get the table value
   1F2A 85 63         [ 3]  518         sta     AGC_GAIN                                ; store this value in AGC_GAIN
   1F2C A5 52         [ 3]  519         lda     TIMER_1MS_C                             ; 10ms timer expired?
   1F2E D0 16         [ 4]  520         bne     $26                                     ; no, just update CPU Leds
   1F30 A9 0A         [ 2]  521         lda     #0x0A
   1F32 85 52         [ 3]  522         sta     TIMER_1MS_C                             ; restart 10ms timer
   1F34 A5 63         [ 3]  523         lda     AGC_GAIN                                ; every 10ms, adjust gain by 1 if needed
   1F36 CD 82 03      [ 4]  524         cmp     audio_periph$ddr_reg_b                  ; compare with current value
   1F39 90 08         [ 4]  525         bcc     $25
   1F3B F0 09         [ 4]  526         beq     $26
   1F3D EE 82 03      [ 6]  527         inc     audio_periph$ddr_reg_b                  ; increase value
   1F40 4C 46 1F      [ 3]  528         jmp     $26
                            529 ;
   1F43                     530 $25:
   1F43 CE 82 03      [ 6]  531         dec     audio_periph$ddr_reg_b                  ; decrease value
   1F46                     532 $26:
   1F46 AD 82 03      [ 4]  533         lda     audio_periph$ddr_reg_b                  ; update CPU leds with value
   1F49 8D 82 02      [ 4]  534         sta     U19_PORTB
   1F4C 60            [ 6]  535         rts
                            536 ;
                            537 ;       AGC table
                            538 ;
   1F4D                     539 AGCTABLE:
   1F4D 03 04 06 08         540         .db     0x03, 0x04, 0x06, 0x08
   1F51 10 16 20 2D         541         .db     0x10, 0x16, 0x20, 0x2D
   1F55 40 5A 80 BF         542         .db     0x40, 0x5A, 0x80, 0xBF
   1F59 FF FF FF FF         543         .db     0xFF, 0xFF, 0xFF, 0xFF
   1F5D FF                  544         .db     0xFF
                            545 ;
                            546 ; all zeros in this gap
                            547 ;
   1F5E 00 00               548         .byte   0x00,0x00
   1F60 00 00 00 00 00 00   549         .byte   0x00,0x00,0x00,0x00,0x00,0x00,0x00,0x00,0x00,0x00,0x00,0x00,0x00,0x00,0x00,0x00
        00 00 00 00 00 00
        00 00 00 00
   1F70 00 00 00 00 00 00   550         .byte   0x00,0x00,0x00,0x00,0x00,0x00,0x00,0x00,0x00,0x00,0x00,0x00,0x00,0x00,0x00,0x00
        00 00 00 00 00 00
        00 00 00 00
   1F80 00 00 00 00 00 00   551         .byte   0x00,0x00,0x00,0x00,0x00,0x00,0x00,0x00,0x00,0x00,0x00,0x00,0x00,0x00,0x00,0x00
        00 00 00 00 00 00
        00 00 00 00
   1F90 00 00 00 00 00 00   552         .byte   0x00,0x00,0x00,0x00,0x00,0x00,0x00,0x00,0x00,0x00,0x00,0x00,0x00,0x00,0x00,0x00
        00 00 00 00 00 00
        00 00 00 00
   1FA0 00 00 00 00 00 00   553         .byte   0x00,0x00,0x00,0x00,0x00,0x00,0x00,0x00,0x00,0x00,0x00,0x00,0x00,0x00,0x00,0x00
        00 00 00 00 00 00
        00 00 00 00
   1FB0 00 00 00 00 00 00   554         .byte   0x00,0x00,0x00,0x00,0x00,0x00,0x00,0x00,0x00,0x00,0x00,0x00,0x00,0x00,0x00,0x00
        00 00 00 00 00 00
        00 00 00 00
   1FC0 00 00 00 00 00 00   555         .byte   0x00,0x00,0x00,0x00,0x00,0x00,0x00,0x00,0x00,0x00,0x00,0x00,0x00,0x00,0x00,0x00
        00 00 00 00 00 00
        00 00 00 00
   1FD0 00 00 00 00 00 00   556         .byte   0x00,0x00,0x00,0x00,0x00,0x00,0x00,0x00,0x00,0x00,0x00,0x00,0x00,0x00,0x00,0x00
        00 00 00 00 00 00
        00 00 00 00
   1FE0 00 00 00 00 00 00   557         .byte   0x00,0x00,0x00,0x00,0x00,0x00,0x00,0x00,0x00,0x00,0x00,0x00,0x00,0x00,0x00,0x00
        00 00 00 00 00 00
        00 00 00 00
   1FF0 00 00 00 00 00 00   558         .byte   0x00,0x00,0x00,0x00,0x00,0x00,0x00,0x00,0x00,0x00
        00 00 00 00
                            559 
   1FFA                     560         .org    0x1FFA
                            561 ;
                            562 ; vectors
                            563 ;
   1FFA                     564 NMIVEC:
   1FFA 00 00               565         .dw     RAM_start
   1FFC                     566 RESETVEC:
   1FFC 00 1C               567         .dw     RESET
   1FFE                     568 IRQVEC:
   1FFE 00 00               569         .dw     RAM_start

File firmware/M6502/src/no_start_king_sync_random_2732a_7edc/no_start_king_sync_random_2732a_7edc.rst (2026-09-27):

                              1 
                              2         .area   region1 (ABS)
                              3 
                     0050     4 TIMER_1MS_A     = 0x0050    ; 1ms timer
                     0051     5 TIMER_1MS_B     = 0x0051    ; 1ms timer
                     0052     6 TIMER_1MS_C     = 0x0052    ; 1ms timer
                     0053     7 TIMER_1MS_R     = 0x0053    ; 1ms timer, autoload to 100
                     0054     8 TIMER_100MS_A   = 0x0054    ; 0.1s timer
                     0055     9 TIMER_100MS_B   = 0x0055    ; 0.1s timer
                     0056    10 TIMER_100MS_R   = 0x0056    ; 0.1s timer, autoload to 100
                     0057    11 TIMER_10S       = 0x0057    ; 10s timer
                     0058    12 ZEROCROSS_CTR   = 0x0058    ; zero crossing counter
                     0059    13 TRACK_CTR       = 0x0059    ; track counter
                             14 
                     005B    15 TAPE_BYTE       = 0x005B    ; storage for incoming serial byte (& 0x7F)
                     005C    16 SOL_MASK        = 0x005C    ; bitmask for solenoids
                     005D    17 CURR_CHANNEL    = 0x005D    ; current channel serial byte
                             18 
                     005F    19 AGC_LEVEL       = 0x005F    ; agc mic level
                     0060    20 AGC_ACCUM       = 0x0060    ; agc mic level accumulator
                     0061    21 AGC_SAMPLES     = 0x0061    ; agc mic sample counter
                     0062    22 AGC_GAIN        = 0x0062    ; agc calculated gain value
                     0063    23 CURR_PORT       = 0x0063    ; current channel port address
                     0064    24 TIMER_100MS_C   = 0x0064    ; 0.1s timer
                     0065    25 KTABLE_OFFS     = 0x0065    ; offset into King table
                     0066    26 KTABLE_SEL      = 0x0066    ; select King table
                     0067    27 UART_RBYTE      = 0x0067    ; UART routine recv byte (0 or 1)
                     0068    28 UART_SBYTE      = 0x0068    ; UART routine send byte (0 or 1)
                     0069    29 UART_ADDR       = 0x0069    ; Address of UART send table (2 bytes)
                             30 
                             31         .include "../../include/ptt6502.def"
                              1 
                              2 ;
                              3 ; Peripheral Addresses for PTT 6502 system
                              4 ;
                              5 
                     0000     6 RAM_start                       = 0x0000
                              7 
                              8 ; Board Select 1
                     0080     9 board_1_periph$ddr_reg_a        = 0x0080
                     0081    10 board_1_control_reg_a           = 0x0081
                     0082    11 board_1_periph$ddr_reg_b        = 0x0082
                     0083    12 board_1_control_reg_b           = 0x0083
                             13 
                             14 ; Board Select 2
                     0084    15 board_2_periph$ddr_reg_a        = 0x0084
                     0086    16 board_2_periph$ddr_reg_b        = 0x0086
                             17 
                             18 ; Board Select 3
                     0088    19 board_3_periph$ddr_reg_a        = 0x0088
                     008A    20 board_3_periph$ddr_reg_b        = 0x008A
                             21 
                             22 ; Board Select 4
                     008C    23 board_4_periph$ddr_reg_a        = 0x008C
                     008E    24 board_4_periph$ddr_reg_b        = 0x008E
                             25 
                             26 ; Board Select 5
                     0090    27 board_5_periph$ddr_reg_a        = 0x0090
                     0092    28 board_5_periph$ddr_reg_b        = 0x0092
                             29 
                             30 ; Board Select 6
                     0094    31 board_6_periph$ddr_reg_a        = 0x0094
                             32 
                             33 ; Board Select 7
                     0098    34 board_7_periph$ddr_reg_a        = 0x0098
                     009A    35 board_7_periph$ddr_reg_b        = 0x009A
                             36 
                             37 ; Board Select 8
                     009C    38 board_8_periph$ddr_reg_a        = 0x009C
                     009E    39 board_8_periph$ddr_reg_b        = 0x009E
                             40 
                             41 ; UART / Board Select 11
                     0101    42 UART_01                         = 0x0101
                     0102    43 UART_02                         = 0x0102
                             44 
                             45 ; 1st 6532 on CPU board
                     0200    46 U18_PORTA                       = 0x0200
                     0201    47 U18_DDRA                        = 0x0201
                     0202    48 U18_PORTB                       = 0x0202
                     0203    49 U18_DDRB                        = 0x0203
                     0204    50 U18_timer                       = 0x0204
                     0205    51 U18_edge_detect_control_DI_pos  = 0x0205
                     0206    52 U18_06                          = 0x0206    
                     0215    53 U18_timer_8T_DI                 = 0x0215
                     0217    54 U18_17                          = 0x0217
                     021C    55 U18_1C                          = 0x021C    ; timer div by 1, enable interrupt
                     021D    56 U18_1D                          = 0x021D    ; timer div by 1, disable interrupt
                             57 
                             58 ; 2nd 6532 on CPU board
                     0280    59 U19_PORTA                       = 0x0280
                     0281    60 U19_DDRA                        = 0x0281
                     0282    61 U19_PORTB                       = 0x0282
                     0283    62 U19_DDRB                        = 0x0283
                     0285    63 U19_edge_detect_control_DI_pos  = 0x0285
                     0286    64 U19_06                          = 0x0286
                             65 
                             66 ; XPRT / Board Select 12
                     0300    67 transport_periph$ddr_reg_a      = 0x0300
                     0301    68 transport_control_reg_a         = 0x0301
                     0302    69 transport_periph$ddr_reg_b      = 0x0302
                     0303    70 transport_control_reg_b         = 0x0303
                             71 
                             72 ; AUDIO / Board Select 13
                     0380    73 audio_periph$ddr_reg_a          = 0x0380
                     0381    74 audio_control_reg_a             = 0x0381
                     0382    75 audio_periph$ddr_reg_b          = 0x0382
                     0383    76 audio_control_reg_b             = 0x0383
                             77 
                             78 ; Tape Commands
                     0010    79 TAPEMODE_STOP                   = 0x10
                     0020    80 TAPEMODE_FFWD                   = 0x20
                     0040    81 TAPEMODE_REWIND                 = 0x40
                     0080    82 TAPEMODE_PLAY                   = 0x80
                             83 
                             84 
                             85 
                             86 
                             87 
                             88 
                             32 
   1000                      33         .org    0x1000
                             34 
                             35 ;
                             36 ;       IRQ handler
                             37 ;
   1000                      38 IRQ:
   1000 48            [ 3]   39         pha
   1001 AD 05 02      [ 4]   40         lda     U18_edge_detect_control_DI_pos          ; clear PA7 flag
   1004 AD 85 02      [ 4]   41         lda     U19_edge_detect_control_DI_pos          ; clear PA7 flag
   1007 A9 7D         [ 2]   42         lda     #0x7D                                   ; expire every 125*8=1000us=1ms
   1009 8D 1D 02      [ 4]   43         sta     U18_1D                                  ; div by 8, enable interrupt
   100C A5 50         [ 3]   44         lda     TIMER_1MS_A                             ; 1ms timer
   100E F0 02         [ 4]   45         beq     $50
   1010 C6 50         [ 5]   46         dec     TIMER_1MS_A
   1012                      47 $50:
   1012 A5 51         [ 3]   48         lda     TIMER_1MS_B                             ; 1ms timer
   1014 F0 02         [ 4]   49         beq     $51
   1016 C6 51         [ 5]   50         dec     TIMER_1MS_B
   1018                      51 $51:
   1018 A5 52         [ 3]   52         lda     TIMER_1MS_C                             ; 1ms timer
   101A F0 02         [ 4]   53         beq     $52
   101C C6 52         [ 5]   54         dec     TIMER_1MS_C
   101E                      55 $52:
   101E C6 53         [ 5]   56         dec     TIMER_1MS_R
   1020 D0 24         [ 4]   57         bne     $56
   1022 A9 64         [ 2]   58         lda     #0x64
   1024 85 53         [ 3]   59         sta     TIMER_1MS_R
   1026 A5 54         [ 3]   60         lda     TIMER_100MS_A
   1028 F0 02         [ 4]   61         beq     $53
   102A C6 54         [ 5]   62         dec     TIMER_100MS_A
   102C                      63 $53:
   102C A5 64         [ 3]   64         lda     TIMER_100MS_C
   102E F0 02         [ 4]   65         beq     $54
   1030 C6 64         [ 5]   66         dec     TIMER_100MS_C
   1032                      67 $54:
   1032 A5 55         [ 3]   68         lda     TIMER_100MS_B
   1034 F0 02         [ 4]   69         beq     $55
   1036 C6 55         [ 5]   70         dec     TIMER_100MS_B
   1038                      71 $55:
   1038 C6 56         [ 5]   72         dec     TIMER_100MS_R
   103A D0 0A         [ 4]   73         bne     $56
   103C A9 64         [ 2]   74         lda     #0x64
   103E 85 56         [ 3]   75         sta     TIMER_100MS_R
   1040 A5 57         [ 3]   76         lda     TIMER_10S
   1042 F0 02         [ 4]   77         beq     $56
   1044 C6 57         [ 5]   78         dec     TIMER_10S
   1046                      79 $56:
   1046 68            [ 4]   80         pla
   1047 40            [ 6]   81         rti
                             82 ;
                             83 ;       Main Program Start
                             84 ;
   1048                      85 RESET:
   1048 D8            [ 2]   86         cld                                             ; No decimal mode
   1049 78            [ 2]   87         sei                                             ; Interrupts are not used
   104A A2 F0         [ 2]   88         ldx     #0xF0                                   ; Stack is at 0x01F0
   104C 9A            [ 2]   89         txs
   104D A9 00         [ 2]   90         lda     #0x00                                   ; Clear RAM
   104F A2 10         [ 2]   91         ldx     #0x10                                   ; from 0x0010 to 0x007F
   1051                      92 ZERORAM:
   1051 95 00         [ 4]   93         sta     0x00,x
   1053 E8            [ 2]   94         inx
   1054 E0 80         [ 2]   95         cpx     #0x80
   1056 D0 F9         [ 4]   96         bne     ZERORAM
   1058 A9 00         [ 2]   97         lda     #0x00
   105A 8D 01 03      [ 4]   98         sta     transport_control_reg_a                 ; Clear transport control A, select DDRA
   105D 8D 00 03      [ 4]   99         sta     transport_periph$ddr_reg_a              ; UART data inputs
   1060 8D 81 03      [ 4]  100         sta     audio_control_reg_a                     ; Clear audio control A, select DDRA
   1063 8D 80 03      [ 4]  101         sta     audio_periph$ddr_reg_a                  ; Comparator inputs
   1066 8D 83 03      [ 4]  102         sta     audio_control_reg_b                     ; Clear audio control B
   1069 8D 05 02      [ 4]  103         sta     U18_edge_detect_control_DI_pos          ; Detect PROG button release
   106C 8D 03 03      [ 4]  104         sta     transport_control_reg_b                 ; Clear transport control B, select DDRB
   106F 8D 06 02      [ 4]  105         sta     U18_06                                  ; ???
   1072 8D 86 02      [ 4]  106         sta     U19_06                                  ; ???
   1075 8D 01 02      [ 4]  107         sta     U18_DDRA                                ; Buttons are inputs
   1078 A9 02         [ 2]  108         lda     #0x02
   107A 8D 81 02      [ 4]  109         sta     U19_DDRA                                ; AGC and MIKESW are inputs, RESET Light output
   107D A9 FF         [ 2]  110         lda     #0xFF
   107F 8D 82 03      [ 4]  111         sta     audio_periph$ddr_reg_b                  ; DAC08 outputs
   1082 8D 03 02      [ 4]  112         sta     U18_DDRB                                ; Button lights are outputs
   1085 8D 83 02      [ 4]  113         sta     U19_DDRB                                ; CPU card lights are outputs
   1088 A9 FC         [ 2]  114         lda     #0xFC
   108A 8D 02 03      [ 4]  115         sta     transport_periph$ddr_reg_b              ; transport control, chip control are outputs, PB1 & PB0 inputs
   108D A9 2E         [ 2]  116         lda     #0x2E
   108F 8D 01 03      [ 4]  117         sta     transport_control_reg_a                 ; transport CA2 is Read strobe (~DDR), set IRQA bit on ~DR low to high 
   1092 8D 03 03      [ 4]  118         sta     transport_control_reg_b                 ; transport CB2 is Write strobe (~THRL), set IRQB bit on CB1 low to high
   1095 A9 3C         [ 2]  119         lda     #0x3C
   1097 8D 81 03      [ 4]  120         sta     audio_control_reg_a                     ; CA2 High - Disable BG Audio
   109A 8D 83 03      [ 4]  121         sta     audio_control_reg_b                     ; CB2 high - Disable Tape Audio
   109D 58            [ 2]  122         cli
   109E 8D 1C 02      [ 4]  123         sta     U18_1C
   10A1 A9 64         [ 2]  124         lda     #0x64
   10A3 85 53         [ 3]  125         sta     TIMER_1MS_R                             ; 100 - init 1 msec master counter
   10A5 A9 18         [ 2]  126         lda     #0x18
   10A7 85 57         [ 3]  127         sta     TIMER_10S                               ; Init a 4 minute timer
   10A9 A9 64         [ 2]  128         lda     #0x64
   10AB 85 56         [ 3]  129         sta     TIMER_100MS_R                           ; 100 - init 0.1 sec master counter
   10AD A9 0A         [ 2]  130         lda     #0x0A                                   ; 10
   10AF 85 62         [ 3]  131         sta     AGC_GAIN                                ; Set initial AGC gain value
   10B1 A9 09         [ 2]  132         lda     #0x09
   10B3 8D 02 01      [ 4]  133         sta     UART_02                                 ; ???
   10B6 A9 10         [ 2]  134         lda     #TAPEMODE_STOP
   10B8 20 2E 12      [ 6]  135         jsr     TAPECMD                                 ; STOP tape
   10BB A9 28         [ 2]  136         lda     #0x28                                   ; this will count 4 seconds
   10BD 85 54         [ 3]  137         sta     TIMER_100MS_A
   10BF A9 64         [ 2]  138         lda     #0x64                                   ; reset master timer
   10C1 85 53         [ 3]  139         sta     TIMER_1MS_R
   10C3                     140 $1:
   10C3 A5 54         [ 3]  141         lda     TIMER_100MS_A                           ; do not much for 4 seconds
   10C5 D0 FC         [ 4]  142         bne     $1
   10C7 20 FB 11      [ 6]  143         jsr     INITBRDS
   10CA                     144 REWIND:
   10CA A9 FA         [ 2]  145         lda     #0xFA
   10CC 85 64         [ 3]  146         sta     TIMER_100MS_C
   10CE A9 00         [ 2]  147         lda     #0x00
   10D0 85 65         [ 3]  148         sta     KTABLE_OFFS
   10D2 85 66         [ 3]  149         sta     KTABLE_SEL
   10D4 A9 30         [ 2]  150         lda     #0x30
   10D6 A9 40         [ 2]  151         lda     #TAPEMODE_REWIND
   10D8 20 2E 12      [ 6]  152         jsr     TAPECMD                                 ; REWIND tape
   10DB                     153 $22:
   10DB A9 00         [ 2]  154         lda     #0x00
   10DD 85 58         [ 3]  155         sta     ZEROCROSS_CTR                           ; counter to zero
   10DF                     156 $3:
   10DF AD 02 03      [ 4]  157         lda     transport_periph$ddr_reg_b
   10E2 A9 0A         [ 2]  158         lda     #0x0A
   10E4 85 50         [ 3]  159         sta     TIMER_1MS_A                             ; set a 10ms timer
   10E6 E6 58         [ 5]  160         inc     ZEROCROSS_CTR                           ; count transitions
   10E8 A5 58         [ 3]  161         lda     ZEROCROSS_CTR
   10EA C9 64         [ 2]  162         cmp     #0x64
   10EC B0 0F         [ 4]  163         bcs     FINDTRK                                 ; happened 100 times, tape is at the beginning, jump ahead
   10EE                     164 $4:
   10EE 20 ED 13      [ 6]  165         jsr     KUPDATE
   10F1 A5 50         [ 3]  166         lda     TIMER_1MS_A
   10F3 F0 E6         [ 4]  167         beq     $22
   10F5 AD 03 03      [ 4]  168         lda     transport_control_reg_b
   10F8 10 F4         [ 4]  169         bpl     $4
   10FA 4C DF 10      [ 3]  170         jmp     $3
                            171 
                            172 ;
   10FD                     173 FINDTRK:
   10FD A9 20         [ 2]  174         lda     #TAPEMODE_FFWD
   10FF 20 2E 12      [ 6]  175         jsr     TAPECMD                                 ; FFWD tape
   1102 A9 19         [ 2]  176         lda     #0x19
   1104 85 54         [ 3]  177         sta     TIMER_100MS_A                           ; 2.5 secs
   1106 A9 64         [ 2]  178         lda     #0x64
   1108 85 53         [ 3]  179         sta     TIMER_1MS_R
   110A                     180 $5:
   110A 20 ED 13      [ 6]  181         jsr     KUPDATE
   110D A5 54         [ 3]  182         lda     TIMER_100MS_A
   110F D0 F9         [ 4]  183         bne     $5
   1111 A9 00         [ 2]  184         lda     #0x00
   1113 85 59         [ 3]  185         sta     TRACK_CTR
   1115 20 49 12      [ 6]  186         jsr     WAITTONE                                ; wait for tone signaling beginning of track
   1118 A9 40         [ 2]  187         lda     #TAPEMODE_REWIND
   111A 20 2E 12      [ 6]  188         jsr     TAPECMD                                 ; REWIND tape
   111D 20 49 12      [ 6]  189         jsr     WAITTONE                                ; wait for tone signaling beginning of track
   1120 A9 FA         [ 2]  190         lda     #0xFA
   1122 85 50         [ 3]  191         sta     TIMER_1MS_A
   1124                     192 $30:
   1124 20 ED 13      [ 6]  193         jsr     KUPDATE
   1127 A5 50         [ 3]  194         lda     TIMER_1MS_A
   1129 D0 F9         [ 4]  195         bne     $30                                     ; delay for 250 ms
   112B A9 20         [ 2]  196         lda     #TAPEMODE_FFWD
   112D 20 2E 12      [ 6]  197         jsr     TAPECMD
   1130 20 49 12      [ 6]  198         jsr     WAITTONE                                ; wait for tone signaling beginning of track
   1133 E6 59         [ 5]  199         inc     TRACK_CTR
   1135 A9 10         [ 2]  200         lda     #TAPEMODE_STOP
   1137 20 2E 12      [ 6]  201         jsr     TAPECMD                                 ; STOP tape
   113A A9 80         [ 2]  202         lda     #TAPEMODE_PLAY
   113C 20 2E 12      [ 6]  203         jsr     TAPECMD                                 ; PLAY tape
   113F 20 6C 12      [ 6]  204         jsr     WAITCD                                  ; wait for carrier
   1142 A9 10         [ 2]  205         lda     #TAPEMODE_STOP
   1144 20 2E 12      [ 6]  206         jsr     TAPECMD                                 ; STOP Tape
   1147                     207 WAITPLAY:
   1147 A9 5E         [ 2]  208         lda     #<UTABLE_M2
   1149 85 69         [ 3]  209         sta     UART_ADDR
   114B A9 13         [ 2]  210         lda     #>UTABLE_M2
   114D 85 6A         [ 3]  211         sta     UART_ADDR+1                             ; set UTABLE address
   114F 20 A9 13      [ 6]  212         jsr     AGCUPD
   1152 20 ED 13      [ 6]  213         jsr     KUPDATE
   1155 20 D3 12      [ 6]  214         jsr     UARTPROC
   1158 AD 02 01      [ 4]  215         lda     UART_02
   115B 29 05         [ 2]  216         and     #0x05
   115D F0 23         [ 4]  217         beq     $46
   115F A5 67         [ 3]  218         lda     UART_RBYTE
   1161 D0 0C         [ 4]  219         bne     $45
   1163 AD 01 01      [ 4]  220         lda     UART_01
   1166 C9 53         [ 2]  221         cmp     #'S                                     ; 'S' - start command?
   1168 D0 18         [ 4]  222         bne     $46
   116A E6 67         [ 5]  223         inc     UART_RBYTE
   116C 4C 82 11      [ 3]  224         jmp     $46
   116F                     225 $45:
   116F A9 00         [ 2]  226         lda     #0x00
   1171 85 67         [ 3]  227         sta     UART_RBYTE
   1173 AD 01 01      [ 4]  228         lda     UART_01
   1176 C9 31         [ 2]  229         cmp     #'1                                     ; '1' - 2nd byte startplay command?
   1178 F0 36         [ 4]  230         beq     STARTPLAY
   117A C9 32         [ 2]  231         cmp     #'2                                     ; '2' - 2nd byte lights command?
   117C F0 0A         [ 4]  232         beq     $47
   117E C9 33         [ 2]  233         cmp     #'3                                     ; '3' - 2nd byte lights command?
   1180 F0 1B         [ 4]  234         beq     $48
   1182                     235 $46:
   1182 4C 47 11      [ 3]  236         jmp     WAITPLAY
   1185 4C CA 10      [ 3]  237         jmp     REWIND
                            238 ; lights to all ones
   1188                     239 $47:
   1188 A9 FF         [ 2]  240         lda     #0xFF
   118A 85 98         [ 3]  241         sta     board_7_periph$ddr_reg_a
   118C 85 9A         [ 3]  242         sta     board_7_periph$ddr_reg_b
   118E 85 9C         [ 3]  243         sta     board_8_periph$ddr_reg_a
   1190 85 9E         [ 3]  244         sta     board_8_periph$ddr_reg_b
   1192 8D 02 02      [ 4]  245         sta     U18_PORTB
   1195 A9 02         [ 2]  246         lda     #0x02
   1197 8D 80 02      [ 4]  247         sta     U19_PORTA
   119A 4C 47 11      [ 3]  248         jmp     WAITPLAY
                            249 ; lights to all zeros
   119D                     250 $48:
   119D A9 00         [ 2]  251         lda     #0x00
   119F 85 98         [ 3]  252         sta     board_7_periph$ddr_reg_a
   11A1 85 9A         [ 3]  253         sta     board_7_periph$ddr_reg_b
   11A3 85 9C         [ 3]  254         sta     board_8_periph$ddr_reg_a
   11A5 85 9E         [ 3]  255         sta     board_8_periph$ddr_reg_b
   11A7 8D 02 02      [ 4]  256         sta     U18_PORTB
   11AA 8D 80 02      [ 4]  257         sta     U19_PORTA
   11AD 4C 47 11      [ 3]  258         jmp     WAITPLAY
                            259 
                            260 ;   we have been started!
   11B0                     261 STARTPLAY:
   11B0 20 FB 11      [ 6]  262         jsr     INITBRDS
   11B3 A9 5C         [ 2]  263         lda     #<UTABLE_M1
   11B5 85 69         [ 3]  264         sta     UART_ADDR
   11B7 A9 13         [ 2]  265         lda     #>UTABLE_M1
   11B9 85 6A         [ 3]  266         sta     UART_ADDR+1                             ; set UTABLE address
   11BB A9 00         [ 2]  267         lda     #0x00
   11BD 8D 80 02      [ 4]  268         sta     U19_PORTA                               ; turn off RESET button light
   11C0 A9 A0         [ 2]  269         lda     #0xA0
   11C2 8D 02 02      [ 4]  270         sta     U18_PORTB                               ; turn off some lights - TBD
   11C5 A9 80         [ 2]  271         lda     #TAPEMODE_PLAY
   11C7 20 2E 12      [ 6]  272         jsr     TAPECMD                                 ; PLAY tape
   11CA 20 6C 12      [ 6]  273         jsr     WAITCD                                  ; wait for carrier
   11CD 20 92 12      [ 6]  274         jsr     PLAYTRK                                 ; play a track!
   11D0 20 FB 11      [ 6]  275         jsr     INITBRDS                                ; init the boards
   11D3 A9 80         [ 2]  276         lda     #0x80
   11D5 8D 02 02      [ 4]  277         sta     U18_PORTB                               ; turn off all but PROG light
   11D8 E6 59         [ 5]  278         inc     TRACK_CTR                               ; track counter
   11DA A5 59         [ 3]  279         lda     TRACK_CTR
   11DC C9 1A         [ 2]  280         cmp     #0x1A                                   ; 26?
   11DE 90 03         [ 4]  281         bcc     NEXTTRK
   11E0 4C CA 10      [ 3]  282         jmp     REWIND                                  ; rewind the tape after the total number of tracks are done
                            283 
   11E3                     284 NEXTTRK:
   11E3 A9 00         [ 2]  285         lda     #0x00
   11E5 85 65         [ 3]  286         sta     KTABLE_OFFS
   11E7 85 66         [ 3]  287         sta     KTABLE_SEL
   11E9 A9 FA         [ 2]  288         lda     #0xFA
   11EB 85 64         [ 3]  289         sta     TIMER_100MS_C
   11ED 20 6C 12      [ 6]  290         jsr     WAITCD                                  ; wait for carrier
   11F0 A9 10         [ 2]  291         lda     #TAPEMODE_STOP
   11F2 20 2E 12      [ 6]  292         jsr     TAPECMD                                 ; STOP tape
   11F5 20 60 13      [ 6]  293         jsr     AGCMICRD                                ; Read the AGC mic level
   11F8 4C 47 11      [ 3]  294         jmp     WAITPLAY
                            295 ;
                            296 ;       Init boards
                            297 ;
   11FB                     298 INITBRDS:
   11FB A9 3C         [ 2]  299         lda     #0x3C
   11FD 8D 83 03      [ 4]  300         sta     audio_control_reg_b                     ; CB2 High (Disable Tape Audio)
   1200 A9 34         [ 2]  301         lda     #0x34
   1202 8D 81 03      [ 4]  302         sta     audio_control_reg_a                     ; CA2 Low (Enable BG Audio)
   1205 A2 00         [ 2]  303         ldx     #0x00
   1207                     304 NEXTBRD:
   1207 A9 30         [ 2]  305         lda     #0x30
   1209 95 81         [ 4]  306         sta     board_1_control_reg_a,x                 ; boardX CA2 low, DDR select
   120B 95 83         [ 4]  307         sta     board_1_control_reg_b,x                 ; boardX CB2 low, DDR select
   120D A9 FF         [ 2]  308         lda     #0xFF
   120F 95 80         [ 4]  309         sta     board_1_periph$ddr_reg_a,x              ; all A pins to outputs
   1211 95 82         [ 4]  310         sta     board_1_periph$ddr_reg_b,x              ; all B pins to outputs
   1213 A9 34         [ 2]  311         lda     #0x34
   1215 95 81         [ 4]  312         sta     board_1_control_reg_a,x                 ; A peripheral selected
   1217 95 83         [ 4]  313         sta     board_1_control_reg_b,x                 ; B peripheral selected
   1219 A9 00         [ 2]  314         lda     #0x00
   121B 95 80         [ 4]  315         sta     board_1_periph$ddr_reg_a,x              ; A solenoids off
   121D 95 82         [ 4]  316         sta     board_1_periph$ddr_reg_b,x              ; B solenoids off
   121F E8            [ 2]  317         inx
   1220 E8            [ 2]  318         inx
   1221 E8            [ 2]  319         inx
   1222 E8            [ 2]  320         inx
   1223 E0 20         [ 2]  321         cpx     #0x20                                   ; do for boards 1-8
   1225 90 E0         [ 4]  322         bcc     NEXTBRD
   1227 A9 00         [ 2]  323         lda     #0x00                                   ; bug fix!
   1229 85 5D         [ 3]  324         sta     CURR_CHANNEL                            ; reset current channel serial byte
   122B 85 63         [ 3]  325         sta     CURR_PORT                               ; reset current channel port address
   122D 60            [ 6]  326         rts
                            327 ;
                            328 ;       Send Transport command for 0.250 sec
                            329 ;       (Unified)
                            330 ;
   122E                     331 TAPECMD:
   122E 8D 02 03      [ 4]  332         sta     transport_periph$ddr_reg_b              ; enable output line
   1231 A9 FA         [ 2]  333         lda     #0xFA
   1233 85 50         [ 3]  334         sta     TIMER_1MS_A
   1235                     335 $6:
   1235 20 ED 13      [ 6]  336         jsr     KUPDATE                                 ; housekeeping
   1238 A5 50         [ 3]  337         lda     TIMER_1MS_A
   123A D0 F9         [ 4]  338         bne     $6
   123C AD 02 03      [ 4]  339         lda     transport_periph$ddr_reg_b
   123F 29 60         [ 2]  340         and     #TAPEMODE_REWIND | #TAPEMODE_FFWD       ; Is it a REWIND or FFWD?
   1241 D0 05         [ 4]  341         bne     $31                                     ; Yes, go to exit
   1243 A9 00         [ 2]  342         lda     #0x00                                   ; else unassert STOP or PLAY
   1245 8D 02 03      [ 4]  343         sta     transport_periph$ddr_reg_b              ; and then exit
   1248                     344 $31:
   1248 60            [ 6]  345         rts
                            346 ;
                            347 ;       Wait for tone during Fast Forward, signaling beginning of track
                            348 ;       (50Hz or above, for 33 zero crossing) 
                            349 ;
   1249                     350 WAITTONE:
   1249 A9 00         [ 2]  351         lda     #0x00
   124B 85 58         [ 3]  352         sta     ZEROCROSS_CTR
   124D                     353 $8:
   124D AD 02 03      [ 4]  354         lda     transport_periph$ddr_reg_b
   1250 A9 0A         [ 2]  355         lda     #0x0A
   1252 85 50         [ 3]  356         sta     TIMER_1MS_A                             ; 10 msec
   1254 E6 58         [ 5]  357         inc     ZEROCROSS_CTR
   1256 A5 58         [ 3]  358         lda     ZEROCROSS_CTR
   1258 C9 21         [ 2]  359         cmp     #0x21                                   ; wait for 33 rising edges, each within 10ms window
   125A B0 0F         [ 4]  360         bcs     $10                                     ; timeout - exit
   125C                     361 $9:
   125C 20 ED 13      [ 6]  362         jsr     KUPDATE
   125F A5 50         [ 3]  363         lda     TIMER_1MS_A
   1261 F0 E6         [ 4]  364         beq     WAITTONE                                ; 10 msec done yet? then loop
   1263 AD 03 03      [ 4]  365         lda     transport_control_reg_b                 ; transport CB1 rising edge?
   1266 10 F4         [ 4]  366         bpl     $9                                      ; if not, extend the looping
   1268 4C 4D 12      [ 3]  367         jmp     $8      
                            368 
   126B                     369 $10:
   126B 60            [ 6]  370         rts
                            371 ;
                            372 ;       Wait for carrier / start of data
                            373 ;
                            374 
                            375 ; Wait for 250ms
   126C                     376 WAITCD:
   126C A9 FA         [ 2]  377         lda     #0xFA
   126E 85 50         [ 3]  378         sta     TIMER_1MS_A                             ; 250 msec
   1270                     379 $11:
   1270 20 ED 13      [ 6]  380         jsr     KUPDATE
   1273 A5 50         [ 3]  381         lda     TIMER_1MS_A
   1275 D0 F9         [ 4]  382         bne     $11
                            383 
                            384 ; Wait for 160ms of consecutive zero crossings
   1277                     385 $12:
   1277 20 ED 13      [ 6]  386         jsr     KUPDATE
   127A AD 02 03      [ 4]  387         lda     transport_periph$ddr_reg_b
   127D 6A            [ 2]  388         ror
   127E 90 F7         [ 4]  389         bcc     $12
   1280 A9 A0         [ 2]  390         lda     #0xA0                                   ; 160 msec
   1282 85 50         [ 3]  391         sta     TIMER_1MS_A
                            392 
                            393 
   1284                     394 $13:
   1284 20 ED 13      [ 6]  395         jsr     KUPDATE
   1287 AD 02 03      [ 4]  396         lda     transport_periph$ddr_reg_b
   128A 6A            [ 2]  397         ror
   128B 90 EA         [ 4]  398         bcc     $12
   128D A5 50         [ 3]  399         lda     TIMER_1MS_A
   128F D0 F3         [ 4]  400         bne     $13
   1291 60            [ 6]  401         rts
                            402 ;
                            403 ;       Play a track
                            404 ;
   1292                     405 PLAYTRK:
   1292 AD 00 03      [ 4]  406         lda     transport_periph$ddr_reg_a
   1295 A9 40         [ 2]  407         lda     #0x40
   1297 85 82         [ 3]  408         sta     board_1_periph$ddr_reg_b                ; only Board 1 PB6 on
   1299 85 86         [ 3]  409         sta     board_2_periph$ddr_reg_b                ; only Board 2 PB6 on
   129B 85 8A         [ 3]  410         sta     board_3_periph$ddr_reg_b                ; only Board 3 PB6 on
   129D 85 8E         [ 3]  411         sta     board_4_periph$ddr_reg_b                ; only Board 4 PB6 on
   129F A9 3C         [ 2]  412         lda     #0x3C
   12A1 8D 81 03      [ 4]  413         sta     audio_control_reg_a                     ; CA2 High (Disable Other Audio)
   12A4 A9 34         [ 2]  414         lda     #0x34
   12A6 8D 83 03      [ 4]  415         sta     audio_control_reg_b                     ; CB2 Low (Enable Tape Audio)
   12A9 A9 60         [ 2]  416         lda     #0x60
   12AB 85 82         [ 3]  417         sta     board_1_periph$ddr_reg_b                ; ???
   12AD                     418 $14:
   12AD AD 02 03      [ 4]  419         lda     transport_periph$ddr_reg_b
   12B0 4A            [ 2]  420         lsr     a
   12B1 90 11         [ 4]  421         bcc     LOSTCD                                  ; b0=0, no carrier, exit
   12B3 20 D3 12      [ 6]  422         jsr     UARTPROC                                ; ??? Unknown UART routine
   12B6 20 A9 13      [ 6]  423         jsr     AGCUPD
   12B9 AD 01 03      [ 4]  424         lda     transport_control_reg_a                 ; Did we get a byte?
   12BC 10 EF         [ 4]  425         bpl     $14                                     ; No, loop
   12BE 20 F3 12      [ 6]  426         jsr     PROTOHAND                               ; Yes, Process Incoming Byte
   12C1 4C AD 12      [ 3]  427         jmp     $14
                            428 
                            429 ;       Lost carrier - wait 100 msec for more data before giving up
   12C4                     430 LOSTCD:
   12C4 A9 64         [ 2]  431         lda     #0x64                                   ; 100 msec
   12C6 85 50         [ 3]  432         sta     TIMER_1MS_A
   12C8                     433 $15:
   12C8 AD 02 03      [ 4]  434         lda     transport_periph$ddr_reg_b
   12CB 4A            [ 2]  435         lsr
   12CC B0 C4         [ 4]  436         bcs     PLAYTRK
   12CE A5 50         [ 3]  437         lda     TIMER_1MS_A
   12D0 D0 F6         [ 4]  438         bne     $15
   12D2 60            [ 6]  439         rts
                            440 ;
                            441 ;   TBD - Unknown UART routine
                            442 ;   Send first or second byte from the UART table to UART_01
                            443 ;
   12D3                     444 UARTPROC:
   12D3 AD 02 01      [ 4]  445         lda     UART_02                                 ; check UART_02.bit2 == 0
   12D6 29 02         [ 2]  446         and     #0x02                                   
   12D8 F0 18         [ 4]  447         beq     $42                                     ; if so, return
   12DA A5 68         [ 3]  448         lda     UART_SBYTE                              ; else, check byte number
   12DC D0 09         [ 4]  449         bne     $40
   12DE A0 00         [ 2]  450         ldy     #0x00
   12E0 B1 69         [ 6]  451         lda     [UART_ADDR],y                           ; send first byte
   12E2 E6 68         [ 5]  452         inc     UART_SBYTE
   12E4 4C EF 12      [ 3]  453         jmp     $41
   12E7                     454 $40:
   12E7 A9 00         [ 2]  455         lda     #0x00
   12E9 85 68         [ 3]  456         sta     UART_SBYTE
   12EB A0 01         [ 2]  457         ldy     #0x01
   12ED B1 69         [ 6]  458         lda     [UART_ADDR],y                           ; send second byte
   12EF                     459 $41:
   12EF 8D 01 01      [ 4]  460         sta     UART_01
   12F2                     461 $42:
   12F2 60            [ 6]  462         rts
                            463 ;
                            464 ; Protocol handler
                            465 ;
   12F3                     466 PROTOHAND:
   12F3 AD 00 03      [ 4]  467         lda     transport_periph$ddr_reg_a
   12F6                     468 PROCBYTE:
   12F6 29 7F         [ 2]  469         and     #0x7F                                   ; insure data is ASCII
   12F8 85 5B         [ 3]  470         sta     TAPE_BYTE                               ; store it here
   12FA 29 7E         [ 2]  471         and     #0x7E                                   ; ignore bottom bit
   12FC C9 22         [ 2]  472         cmp     #0x22                                   ; is it 0x22 or 0x23?
   12FE F0 3A         [ 4]  473         beq     PROCCHNL                                ; if so, process as channel
   1300 C9 32         [ 2]  474         cmp     #0x32                                   ; is it < 0x32 ?
   1302 90 4F         [ 4]  475         bcc     $18                                     ; ignore it
   1304 C9 3A         [ 2]  476         cmp     #0x3A                                   ; is it < 0x3A
   1306 90 32         [ 4]  477         bcc     PROCCHNL                                ; process as channel (0x32 to 0x39)
   1308 A5 5B         [ 3]  478         lda     TAPE_BYTE
   130A C9 41         [ 2]  479         cmp     #0x41                                   ; is it < 0x41?
   130C 90 45         [ 4]  480         bcc     $18                                     ; ignore it
   130E C9 4F         [ 2]  481         cmp     #0x4F                                   ; is it >= 0x4F?
   1310 B0 41         [ 4]  482         bcs     $18                                     ; ignore it
   1312 A6 63         [ 3]  483         ldx     CURR_PORT                               ; X = current board address
   1314 38            [ 2]  484         sec                                             ; (it's 0x41 to 0x4E)
   1315 E9 41         [ 2]  485         sbc     #0x41                                   ; subtract 0x41
   1317 C9 08         [ 2]  486         cmp     #0x08
   1319 90 02         [ 4]  487         bcc     $16                                     ; process as command
   131B E8            [ 2]  488         inx
   131C E8            [ 2]  489         inx
   131D                     490 $16:
   131D 29 07         [ 2]  491         and     #0x07                                   ; lookup bitmask in A
   131F A8            [ 2]  492         tay
   1320 B9 54 13      [ 5]  493         lda     MASKTBL,y
   1323 85 5C         [ 3]  494         sta     SOL_MASK                                ; store mask in SOL_MASK
   1325 A5 5D         [ 3]  495         lda     CURR_CHANNEL
   1327 4A            [ 2]  496         lsr     a                                       ; get on/off in carry
   1328 B0 09         [ 4]  497         bcs     $17                                     ; if on, jump
   132A A5 5C         [ 3]  498         lda     SOL_MASK
   132C 49 FF         [ 2]  499         eor     #0xFF
   132E 35 00         [ 4]  500         and     RAM_start,x
   1330 95 00         [ 4]  501         sta     RAM_start,x                             ; turn off solenoid
   1332 60            [ 6]  502         rts
                            503 ;
   1333                     504 $17:
   1333 A5 5C         [ 3]  505         lda     SOL_MASK
   1335 15 00         [ 4]  506         ora     RAM_start,x
   1337 95 00         [ 4]  507         sta     RAM_start,x                             ; turn on solenoid
   1339 60            [ 6]  508         rts
                            509 ;
   133A                     510 PROCCHNL:
   133A A5 5B         [ 3]  511         lda     TAPE_BYTE                               ; put channel byte in CURR_CHANNEL
   133C 85 5D         [ 3]  512         sta     CURR_CHANNEL
   133E 29 7E         [ 2]  513         and     #0x7E
   1340 C9 22         [ 2]  514         cmp     #0x22
   1342 D0 05         [ 4]  515         bne     CONVCHNL
   1344 A9 98         [ 2]  516         lda     #0x98                                   ; process 0x22 or 0x23
   1346 85 63         [ 3]  517         sta     CURR_PORT                               ; set this to 0x98 - board 7
   1348 60            [ 6]  518         rts
                            519 ;
   1349                     520 CONVCHNL:
   1349 38            [ 2]  521         sec                                             ; process channel
   134A E9 32         [ 2]  522         sbc     #0x32
   134C 0A            [ 2]  523         asl     a
   134D 18            [ 2]  524         clc
   134E 69 80         [ 2]  525         adc     #0x80
   1350 85 63         [ 3]  526         sta     CURR_PORT                               ; (X-0x32) * 2 + 0x80
   1352 60            [ 6]  527         rts
   1353                     528 $18:
   1353 60            [ 6]  529         rts
                            530 ;
                            531 ; bit mask table
                            532 ;
   1354                     533 MASKTBL:
   1354 01 02 04 08         534         .byte   0x01,0x02,0x04,0x08
   1358 10 20 40 80         535         .byte   0x10,0x20,0x40,0x80
                            536 ;
                            537 ; This table is referenced by UART code
                            538 ;
   135C                     539 UTABLE_M1:
   135C 4D 31               540         .byte   'M,'1                                   ; M1
   135E                     541 UTABLE_M2:
   135E 4D 32               542         .byte   'M,'2                                   ; M2
                            543 ;
                            544 ;       Read the AGC mic level
                            545 ;       Take the average of 8 samples, and put it into AGC_LEVEL (range is 0 to 8)
                            546 ;
   1360                     547 AGCMICRD:
   1360 A9 00         [ 2]  548         lda     #0x00
   1362 85 60         [ 3]  549         sta     AGC_ACCUM                               ; init final agc value
   1364 85 61         [ 3]  550         sta     AGC_SAMPLES                             ; init agc sample counter
   1366 A9 0A         [ 2]  551         lda     #0x0A
   1368 85 54         [ 3]  552         sta     TIMER_100MS_A                           ; Start a 1 second timer
   136A A9 64         [ 2]  553         lda     #0x64
   136C 85 53         [ 3]  554         sta     TIMER_1MS_R
   136E                     555 $23:
   136E 20 ED 13      [ 6]  556         jsr     KUPDATE                                 ; housekeeping
   1371 A5 54         [ 3]  557         lda     TIMER_100MS_A
   1373 D0 F9         [ 4]  558         bne     $23                                     ; if 1 sec, do housekeeping
   1375 A9 0A         [ 2]  559         lda     #0x0A
   1377 85 54         [ 3]  560         sta     TIMER_100MS_A
   1379 A9 64         [ 2]  561         lda     #0x64
   137B 85 53         [ 3]  562         sta     TIMER_1MS_R                             ; reset timer
   137D A5 61         [ 3]  563         lda     AGC_SAMPLES
   137F C9 08         [ 2]  564         cmp     #0x08                                   ; 8 samples?
   1381 F0 15         [ 4]  565         beq     $27
   1383 E6 61         [ 5]  566         inc     AGC_SAMPLES                             ; increment the sample counter
   1385 A2 09         [ 2]  567         ldx     #0x09
   1387 38            [ 2]  568         sec
   1388 AD 80 03      [ 4]  569         lda     audio_periph$ddr_reg_a                  ; read the agc mic level
   138B                     570 $24:                                                    ; read the most significant high bit
   138B 2A            [ 2]  571         rol     a
   138C CA            [ 2]  572         dex
   138D 90 FC         [ 4]  573         bcc     $24
   138F 18            [ 2]  574         clc
   1390 8A            [ 2]  575         txa                                             ; 8=high bit7, 0=no high bits
   1391 65 60         [ 3]  576         adc     AGC_ACCUM                               ; add it into AGC_ACCUM (do this 8 times)
   1393 85 60         [ 3]  577         sta     AGC_ACCUM
   1395 4C 6E 13      [ 3]  578         jmp     $23
                            579 ;
   1398                     580 $27:
   1398 46 60         [ 5]  581         lsr     AGC_ACCUM                               ; divide by 8 (average of 8 samples)
   139A 46 60         [ 5]  582         lsr     AGC_ACCUM
   139C 46 60         [ 5]  583         lsr     AGC_ACCUM
   139E A5 60         [ 3]  584         lda     AGC_ACCUM
   13A0 85 5F         [ 3]  585         sta     AGC_LEVEL                               ; store agc value in AGC_LEVEL
   13A2 A9 00         [ 2]  586         lda     #0x00
   13A4 85 60         [ 3]  587         sta     AGC_ACCUM                               ; clear these 2 and return
   13A6 85 61         [ 3]  588         sta     AGC_SAMPLES
   13A8 60            [ 6]  589         rts
                            590 ;
                            591 ;        Do AGC Mic Logic
                            592 ;
   13A9                     593 AGCUPD:
   13A9 AD 80 02      [ 4]  594         lda     U19_PORTA                               ; read AGC knob
   13AC 49 FF         [ 2]  595         eor     #0xFF                                   ; invert the bits
   13AE 4A            [ 2]  596         lsr     a                                       ; get into lower nibble
   13AF 4A            [ 2]  597         lsr     a
   13B0 4A            [ 2]  598         lsr     a
   13B1 4A            [ 2]  599         lsr     a
   13B2 18            [ 2]  600         clc
   13B3 65 5F         [ 3]  601         adc     AGC_LEVEL                               ; add audio level to it
   13B5 AA            [ 2]  602         tax
   13B6 BD DC 13      [ 5]  603         lda     AGCTABLE,x                              ; and get the table value
   13B9 85 62         [ 3]  604         sta     AGC_GAIN                                ; store this value in AGC_GAIN
   13BB A5 52         [ 3]  605         lda     TIMER_1MS_C                             ; 10ms timer expired?
   13BD D0 16         [ 4]  606         bne     $26                                     ; no, just update CPU Leds
   13BF A9 0A         [ 2]  607         lda     #0x0A
   13C1 85 52         [ 3]  608         sta     TIMER_1MS_C                             ; restart 10ms timer
   13C3 A5 62         [ 3]  609         lda     AGC_GAIN                                ; every 10ms, adjust gain by 1 if needed
   13C5 CD 82 03      [ 4]  610         cmp     audio_periph$ddr_reg_b                  ; compare with current value
   13C8 90 08         [ 4]  611         bcc     $25
   13CA F0 09         [ 4]  612         beq     $26
   13CC EE 82 03      [ 6]  613         inc     audio_periph$ddr_reg_b                  ; increase value
   13CF 4C D5 13      [ 3]  614         jmp     $26
                            615 ;
   13D2                     616 $25:
   13D2 CE 82 03      [ 6]  617         dec     audio_periph$ddr_reg_b                  ; decrease value
   13D5                     618 $26:
   13D5 AD 82 03      [ 4]  619         lda     audio_periph$ddr_reg_b                  ; update CPU leds with value
   13D8 8D 82 02      [ 4]  620         sta     U19_PORTB
   13DB 60            [ 6]  621         rts
                            622 ;
                            623 ;       AGC table
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

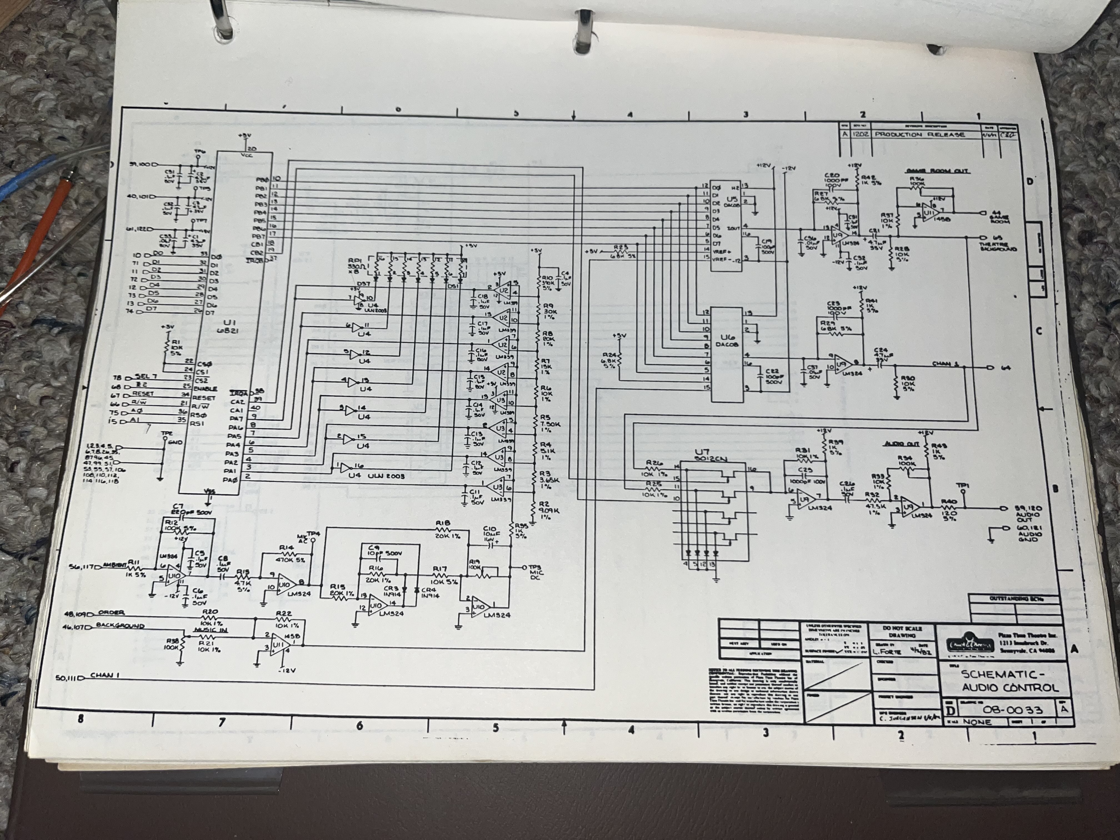
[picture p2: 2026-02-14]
docs/schematics/audio_board_0033.jpg

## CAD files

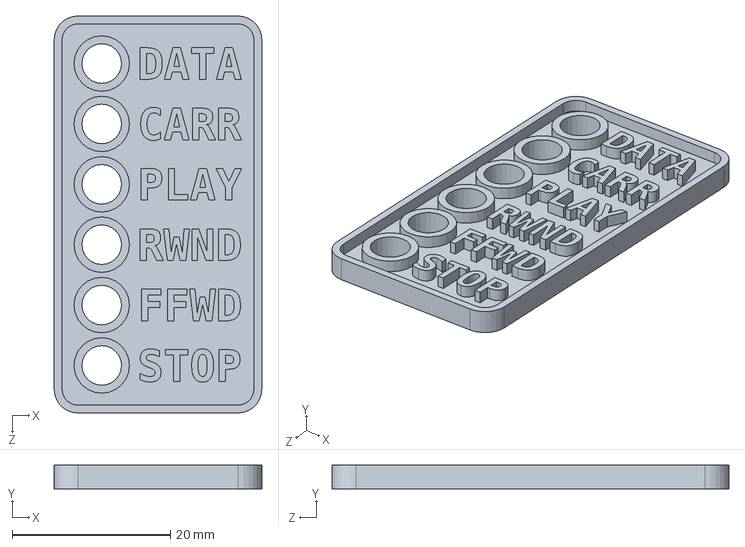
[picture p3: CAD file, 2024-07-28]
3D models/transport card labels.SLDPRT
26.2 x 3.00 x 50.1 mm

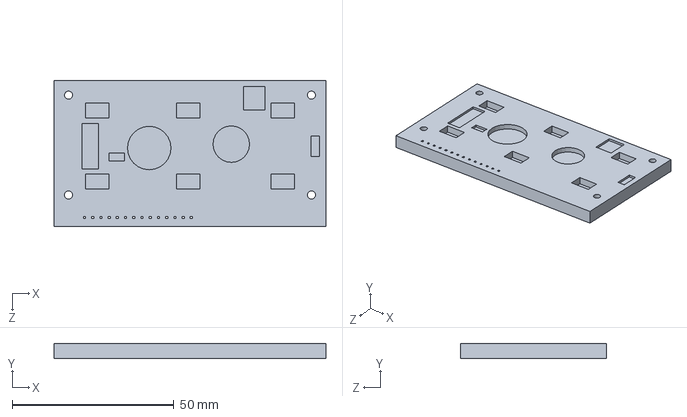
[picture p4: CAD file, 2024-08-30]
Adapters/CEC LCD Adapter.SLDPRT
84.0 x 4.61 x 45.0 mm

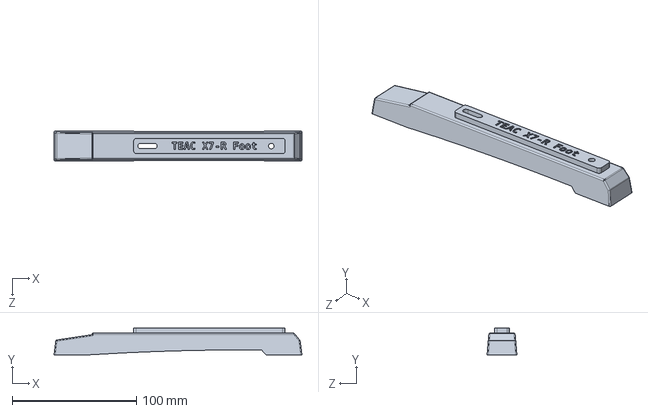
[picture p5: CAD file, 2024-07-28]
3D models/TEAC X7-R foot.SLDPRT
199.5 x 21.3 x 24.0 mm

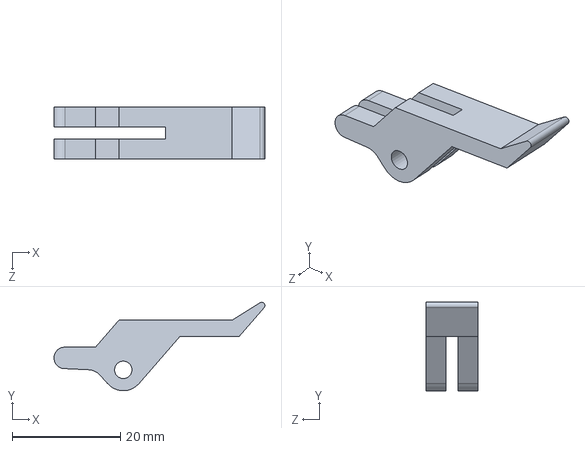
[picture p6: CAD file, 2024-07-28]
3D models/CEC ejector.SLDPRT
38.9 x 16.3 x 9.62 mm

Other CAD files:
3D models/CEC ejector.STL
3D models/TEAC X7-R foot.STL
3D models/transport card labels.STL
Adapters/CEC LCD Adapter.STL

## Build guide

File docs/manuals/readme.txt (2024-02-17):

The HC11 manual is the upgrade manual, and containes schematics for the HC11 CPU, transport interface, and newer versions fo the driver cards.
The Cyberamic Parts manual has some scans drawings of the Control System parts, near the middle of the doc.

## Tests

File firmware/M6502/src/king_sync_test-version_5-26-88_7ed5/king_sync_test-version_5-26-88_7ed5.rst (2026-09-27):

                              1 
                              2         .area   region1 (ABS)
                              3 
                     0050     4 TIMER_1MS_A     = 0x0050    ; 1ms timer
                     0051     5 TIMER_1MS_B     = 0x0051    ; 1ms timer
                     0052     6 TIMER_1MS_C     = 0x0052    ; 1ms timer
                     0053     7 TIMER_1MS_R     = 0x0053    ; 1ms timer, autoload to 100
                     0054     8 TIMER_100MS_A   = 0x0054    ; 0.1s timer
                     0055     9 TIMER_100MS_B   = 0x0055    ; 0.1s timer
                     0056    10 TIMER_100MS_R   = 0x0056    ; 0.1s timer, autoload to 100
                     0057    11 TIMER_10S       = 0x0057    ; 10s timer
                     0058    12 ZEROCROSS_CTR   = 0x0058    ; zero crossing counter
                     0059    13 TRACK_CTR       = 0x0059    ; track counter
                             14 
                     005B    15 TAPE_BYTE       = 0x005B    ; storage for incoming serial byte (& 0x7F)
                     005C    16 SOL_MASK        = 0x005C    ; bitmask for solenoids
                     005D    17 CURR_CHANNEL    = 0x005D    ; current channel serial byte
                             18 
                     005F    19 AGC_LEVEL       = 0x005F    ; agc mic level
                     0060    20 AGC_ACCUM       = 0x0060    ; agc mic level accumulator
                     0061    21 AGC_SAMPLES     = 0x0061    ; agc mic sample counter
                     0062    22 AGC_GAIN        = 0x0062    ; agc calculated gain value
                     0063    23 CURR_PORT       = 0x0063    ; current channel port address
                     0064    24 TIMER_100MS_C   = 0x0064    ; 0.1s timer
                     0065    25 KTABLE_OFFS     = 0x0065    ; offset into King table
                     0066    26 KTABLE_SEL      = 0x0066    ; select King table
                     0067    27 UART_RBYTE      = 0x0067    ; UART routine recv byte (0 or 1)
                     0068    28 UART_SBYTE      = 0x0068    ; UART routine send byte (0 or 1)
                     0069    29 UART_ADDR       = 0x0069    ; Address of UART send table (2 bytes)
                             30 
                             31         .include "../../include/ptt6502.def"
                              1 
                              2 ;
                              3 ; Peripheral Addresses for PTT 6502 system
                              4 ;
                              5 
                     0000     6 RAM_start                       = 0x0000
                              7 
                              8 ; Board Select 1
                     0080     9 board_1_periph$ddr_reg_a        = 0x0080
                     0081    10 board_1_control_reg_a           = 0x0081
                     0082    11 board_1_periph$ddr_reg_b        = 0x0082
                     0083    12 board_1_control_reg_b           = 0x0083
                             13 
                             14 ; Board Select 2
                     0084    15 board_2_periph$ddr_reg_a        = 0x0084
                     0086    16 board_2_periph$ddr_reg_b        = 0x0086
                             17 
                             18 ; Board Select 3
                     0088    19 board_3_periph$ddr_reg_a        = 0x0088
                     008A    20 board_3_periph$ddr_reg_b        = 0x008A
                             21 
                             22 ; Board Select 4
                     008C    23 board_4_periph$ddr_reg_a        = 0x008C
                     008E    24 board_4_periph$ddr_reg_b        = 0x008E
                             25 
                             26 ; Board Select 5
                     0090    27 board_5_periph$ddr_reg_a        = 0x0090
                     0092    28 board_5_periph$ddr_reg_b        = 0x0092
                             29 
                             30 ; Board Select 6
                     0094    31 board_6_periph$ddr_reg_a        = 0x0094
                             32 
                             33 ; Board Select 7
                     0098    34 board_7_periph$ddr_reg_a        = 0x0098
                     009A    35 board_7_periph$ddr_reg_b        = 0x009A
                             36 
                             37 ; Board Select 8
                     009C    38 board_8_periph$ddr_reg_a        = 0x009C
                     009E    39 board_8_periph$ddr_reg_b        = 0x009E
                             40 
                             41 ; UART / Board Select 11
                     0101    42 UART_01                         = 0x0101
                     0102    43 UART_02                         = 0x0102
                             44 
                             45 ; 1st 6532 on CPU board
                     0200    46 U18_PORTA                       = 0x0200
                     0201    47 U18_DDRA                        = 0x0201
                     0202    48 U18_PORTB                       = 0x0202
                     0203    49 U18_DDRB                        = 0x0203
                     0204    50 U18_timer                       = 0x0204
                     0205    51 U18_edge_detect_control_DI_pos  = 0x0205
                     0206    52 U18_06                          = 0x0206    
                     0215    53 U18_timer_8T_DI                 = 0x0215
                     0217    54 U18_17                          = 0x0217
                     021C    55 U18_1C                          = 0x021C    ; timer div by 1, enable interrupt
                     021D    56 U18_1D                          = 0x021D    ; timer div by 1, disable interrupt
                             57 
                             58 ; 2nd 6532 on CPU board
                     0280    59 U19_PORTA                       = 0x0280
                     0281    60 U19_DDRA                        = 0x0281
                     0282    61 U19_PORTB                       = 0x0282
                     0283    62 U19_DDRB                        = 0x0283
                     0285    63 U19_edge_detect_control_DI_pos  = 0x0285
                     0286    64 U19_06                          = 0x0286
                             65 
                             66 ; XPRT / Board Select 12
                     0300    67 transport_periph$ddr_reg_a      = 0x0300
                     0301    68 transport_control_reg_a         = 0x0301
                     0302    69 transport_periph$ddr_reg_b      = 0x0302
                     0303    70 transport_control_reg_b         = 0x0303
                             71 
                             72 ; AUDIO / Board Select 13
                     0380    73 audio_periph$ddr_reg_a          = 0x0380
                     0381    74 audio_control_reg_a             = 0x0381
                     0382    75 audio_periph$ddr_reg_b          = 0x0382
                     0383    76 audio_control_reg_b             = 0x0383
                             77 
                             78 ; Tape Commands
                     0010    79 TAPEMODE_STOP                   = 0x10
                     0020    80 TAPEMODE_FFWD                   = 0x20
                     0040    81 TAPEMODE_REWIND                 = 0x40
                     0080    82 TAPEMODE_PLAY                   = 0x80
                             83 
                             84 
                             85 
                             86 
                             87 
                             88 
                             32 
   1000                      33         .org    0x1000
                             34 
                             35 ;
                             36 ;       IRQ handler
                             37 ;
   1000                      38 IRQ:
   1000 48            [ 3]   39         pha
   1001 AD 05 02      [ 4]   40         lda     U18_edge_detect_control_DI_pos          ; clear PA7 flag
   1004 AD 85 02      [ 4]   41         lda     U19_edge_detect_control_DI_pos          ; clear PA7 flag
   1007 A9 7D         [ 2]   42         lda     #0x7D                                   ; expire every 125*8=1000us=1ms
   1009 8D 1D 02      [ 4]   43         sta     U18_1D                                  ; div by 8, enable interrupt
   100C A5 50         [ 3]   44         lda     TIMER_1MS_A                             ; 1ms timer
   100E F0 02         [ 4]   45         beq     $50
   1010 C6 50         [ 5]   46         dec     TIMER_1MS_A
   1012                      47 $50:
   1012 A5 51         [ 3]   48         lda     TIMER_1MS_B                             ; 1ms timer
   1014 F0 02         [ 4]   49         beq     $51
   1016 C6 51         [ 5]   50         dec     TIMER_1MS_B
   1018                      51 $51:
   1018 A5 52         [ 3]   52         lda     TIMER_1MS_C                             ; 1ms timer
   101A F0 02         [ 4]   53         beq     $52
   101C C6 52         [ 5]   54         dec     TIMER_1MS_C
   101E                      55 $52:
   101E C6 53         [ 5]   56         dec     TIMER_1MS_R
   1020 D0 24         [ 4]   57         bne     $56
   1022 A9 64         [ 2]   58         lda     #0x64
   1024 85 53         [ 3]   59         sta     TIMER_1MS_R
   1026 A5 54         [ 3]   60         lda     TIMER_100MS_A
   1028 F0 02         [ 4]   61         beq     $53
   102A C6 54         [ 5]   62         dec     TIMER_100MS_A
   102C                      63 $53:
   102C A5 64         [ 3]   64         lda     TIMER_100MS_C
   102E F0 02         [ 4]   65         beq     $54
   1030 C6 64         [ 5]   66         dec     TIMER_100MS_C
   1032                      67 $54:
   1032 A5 55         [ 3]   68         lda     TIMER_100MS_B
   1034 F0 02         [ 4]   69         beq     $55
   1036 C6 55         [ 5]   70         dec     TIMER_100MS_B
   1038                      71 $55:
   1038 C6 56         [ 5]   72         dec     TIMER_100MS_R
   103A D0 0A         [ 4]   73         bne     $56
   103C A9 64         [ 2]   74         lda     #0x64
   103E 85 56         [ 3]   75         sta     TIMER_100MS_R
   1040 A5 57         [ 3]   76         lda     TIMER_10S
   1042 F0 02         [ 4]   77         beq     $56
   1044 C6 57         [ 5]   78         dec     TIMER_10S
   1046                      79 $56:
   1046 68            [ 4]   80         pla
   1047 40            [ 6]   81         rti
                             82 ;
                             83 ;       Main Program Start
                             84 ;
   1048                      85 RESET:
   1048 D8            [ 2]   86         cld                                             ; No decimal mode
   1049 78            [ 2]   87         sei                                             ; Interrupts are not used
   104A A2 F0         [ 2]   88         ldx     #0xF0                                   ; Stack is at 0x01F0
   104C 9A            [ 2]   89         txs
   104D A9 00         [ 2]   90         lda     #0x00                                   ; Clear RAM
   104F A2 10         [ 2]   91         ldx     #0x10                                   ; from 0x0010 to 0x007F
   1051                      92 ZERORAM:
   1051 95 00         [ 4]   93         sta     0x00,x
   1053 E8            [ 2]   94         inx
   1054 E0 80         [ 2]   95         cpx     #0x80
   1056 D0 F9         [ 4]   96         bne     ZERORAM
   1058 A9 00         [ 2]   97         lda     #0x00
   105A 8D 01 03      [ 4]   98         sta     transport_control_reg_a                 ; Clear transport control A, select DDRA
   105D 8D 00 03      [ 4]   99         sta     transport_periph$ddr_reg_a              ; UART data inputs
   1060 8D 81 03      [ 4]  100         sta     audio_control_reg_a                     ; Clear audio control A, select DDRA
   1063 8D 80 03      [ 4]  101         sta     audio_periph$ddr_reg_a                  ; Comparator inputs
   1066 8D 83 03      [ 4]  102         sta     audio_control_reg_b                     ; Clear audio control B
   1069 8D 05 02      [ 4]  103         sta     U18_edge_detect_control_DI_pos          ; Detect PROG button release
   106C 8D 03 03      [ 4]  104         sta     transport_control_reg_b                 ; Clear transport control B, select DDRB
   106F 8D 06 02      [ 4]  105         sta     U18_06                                  ; ???
   1072 8D 86 02      [ 4]  106         sta     U19_06                                  ; ???
   1075 8D 01 02      [ 4]  107         sta     U18_DDRA                                ; Buttons are inputs
   1078 A9 02         [ 2]  108         lda     #0x02
   107A 8D 81 02      [ 4]  109         sta     U19_DDRA                                ; AGC and MIKESW are inputs, RESET Light output
   107D A9 FF         [ 2]  110         lda     #0xFF
   107F 8D 82 03      [ 4]  111         sta     audio_periph$ddr_reg_b                  ; DAC08 outputs
   1082 8D 03 02      [ 4]  112         sta     U18_DDRB                                ; Button lights are outputs
   1085 8D 83 02      [ 4]  113         sta     U19_DDRB                                ; CPU card lights are outputs
   1088 A9 FC         [ 2]  114         lda     #0xFC
   108A 8D 02 03      [ 4]  115         sta     transport_periph$ddr_reg_b              ; transport control, chip control are outputs, PB1 & PB0 inputs
   108D A9 2E         [ 2]  116         lda     #0x2E
   108F 8D 01 03      [ 4]  117         sta     transport_control_reg_a                 ; transport CA2 is Read strobe (~DDR), set IRQA bit on ~DR low to high 
   1092 8D 03 03      [ 4]  118         sta     transport_control_reg_b                 ; transport CB2 is Write strobe (~THRL), set IRQB bit on CB1 low to high
   1095 A9 3C         [ 2]  119         lda     #0x3C
   1097 8D 81 03      [ 4]  120         sta     audio_control_reg_a                     ; CA2 High - Disable BG Audio
   109A 8D 83 03      [ 4]  121         sta     audio_control_reg_b                     ; CB2 high - Disable Tape Audio
   109D 58            [ 2]  122         cli
   109E 8D 1C 02      [ 4]  123         sta     U18_1C
   10A1 A9 64         [ 2]  124         lda     #0x64
   10A3 85 53         [ 3]  125         sta     TIMER_1MS_R                             ; 100 - init 1 msec master counter
   10A5 A9 18         [ 2]  126         lda     #0x18
   10A7 85 57         [ 3]  127         sta     TIMER_10S                               ; Init a 4 minute timer
   10A9 A9 64         [ 2]  128         lda     #0x64
   10AB 85 56         [ 3]  129         sta     TIMER_100MS_R                           ; 100 - init 0.1 sec master counter
   10AD A9 0A         [ 2]  130         lda     #0x0A                                   ; 10
   10AF 85 62         [ 3]  131         sta     AGC_GAIN                                ; Set initial AGC gain value
   10B1 A9 09         [ 2]  132         lda     #0x09
   10B3 8D 02 01      [ 4]  133         sta     UART_02                                 ; ???
   10B6 A9 10         [ 2]  134         lda     #TAPEMODE_STOP
   10B8 20 2E 12      [ 6]  135         jsr     TAPECMD                                 ; STOP tape
   10BB A9 28         [ 2]  136         lda     #0x28                                   ; this will count 4 seconds
   10BD 85 54         [ 3]  137         sta     TIMER_100MS_A
   10BF A9 64         [ 2]  138         lda     #0x64                                   ; reset master timer
   10C1 85 53         [ 3]  139         sta     TIMER_1MS_R
   10C3                     140 $1:
   10C3 A5 54         [ 3]  141         lda     TIMER_100MS_A                           ; do not much for 4 seconds
   10C5 D0 FC         [ 4]  142         bne     $1
   10C7 20 FB 11      [ 6]  143         jsr     INITBRDS
   10CA                     144 REWIND:
   10CA A9 FA         [ 2]  145         lda     #0xFA
   10CC 85 64         [ 3]  146         sta     TIMER_100MS_C
   10CE A9 00         [ 2]  147         lda     #0x00
   10D0 85 65         [ 3]  148         sta     KTABLE_OFFS
   10D2 85 66         [ 3]  149         sta     KTABLE_SEL
   10D4 A9 30         [ 2]  150         lda     #0x30
   10D6 A9 40         [ 2]  151         lda     #TAPEMODE_REWIND
   10D8 20 2E 12      [ 6]  152         jsr     TAPECMD                                 ; REWIND tape
   10DB                     153 $22:
   10DB A9 00         [ 2]  154         lda     #0x00
   10DD 85 58         [ 3]  155         sta     ZEROCROSS_CTR                           ; counter to zero
   10DF                     156 $3:
   10DF AD 02 03      [ 4]  157         lda     transport_periph$ddr_reg_b
   10E2 A9 0A         [ 2]  158         lda     #0x0A
   10E4 85 50         [ 3]  159         sta     TIMER_1MS_A                             ; set a 10ms timer
   10E6 E6 58         [ 5]  160         inc     ZEROCROSS_CTR                           ; count transitions
   10E8 A5 58         [ 3]  161         lda     ZEROCROSS_CTR
   10EA C9 64         [ 2]  162         cmp     #0x64
   10EC B0 0F         [ 4]  163         bcs     FINDTRK                                 ; happened 100 times, tape is at the beginning, jump ahead
   10EE                     164 $4:
   10EE 20 ED 13      [ 6]  165         jsr     KUPDATE
   10F1 A5 50         [ 3]  166         lda     TIMER_1MS_A
   10F3 F0 E6         [ 4]  167         beq     $22
   10F5 AD 03 03      [ 4]  168         lda     transport_control_reg_b
   10F8 10 F4         [ 4]  169         bpl     $4
   10FA 4C DF 10      [ 3]  170         jmp     $3
                            171 
                            172 ;
   10FD                     173 FINDTRK:
   10FD A9 20         [ 2]  174         lda     #TAPEMODE_FFWD
   10FF 20 2E 12      [ 6]  175         jsr     TAPECMD                                 ; FFWD tape
   1102 A9 19         [ 2]  176         lda     #0x19
   1104 85 54         [ 3]  177         sta     TIMER_100MS_A                           ; 2.5 secs
   1106 A9 64         [ 2]  178         lda     #0x64
   1108 85 53         [ 3]  179         sta     TIMER_1MS_R
   110A                     180 $5:
   110A 20 ED 13      [ 6]  181         jsr     KUPDATE
   110D A5 54         [ 3]  182         lda     TIMER_100MS_A
   110F D0 F9         [ 4]  183         bne     $5
   1111 A9 00         [ 2]  184         lda     #0x00
   1113 85 59         [ 3]  185         sta     TRACK_CTR
   1115 20 49 12      [ 6]  186         jsr     WAITTONE                                ; wait for tone signaling beginning of track
   1118 A9 40         [ 2]  187         lda     #TAPEMODE_REWIND
   111A 20 2E 12      [ 6]  188         jsr     TAPECMD                                 ; REWIND tape
   111D 20 49 12      [ 6]  189         jsr     WAITTONE                                ; wait for tone signaling beginning of track
   1120 A9 FA         [ 2]  190         lda     #0xFA
   1122 85 50         [ 3]  191         sta     TIMER_1MS_A
   1124                     192 $30:
   1124 20 ED 13      [ 6]  193         jsr     KUPDATE
   1127 A5 50         [ 3]  194         lda     TIMER_1MS_A
   1129 D0 F9         [ 4]  195         bne     $30                                     ; delay for 250 ms
   112B A9 20         [ 2]  196         lda     #TAPEMODE_FFWD
   112D 20 2E 12      [ 6]  197         jsr     TAPECMD
   1130 20 49 12      [ 6]  198         jsr     WAITTONE                                ; wait for tone signaling beginning of track
   1133 E6 59         [ 5]  199         inc     TRACK_CTR
   1135 A9 10         [ 2]  200         lda     #TAPEMODE_STOP
   1137 20 2E 12      [ 6]  201         jsr     TAPECMD                                 ; STOP tape
   113A A9 80         [ 2]  202         lda     #TAPEMODE_PLAY
   113C 20 2E 12      [ 6]  203         jsr     TAPECMD                                 ; PLAY tape
   113F 20 6C 12      [ 6]  204         jsr     WAITCD                                  ; wait for carrier
   1142 A9 10         [ 2]  205         lda     #TAPEMODE_STOP
   1144 20 2E 12      [ 6]  206         jsr     TAPECMD                                 ; STOP Tape
   1147                     207 WAITPLAY:
   1147 A9 5E         [ 2]  208         lda     #<UTABLE_M2
   1149 85 69         [ 3]  209         sta     UART_ADDR
   114B A9 13         [ 2]  210         lda     #>UTABLE_M2
   114D 85 6A         [ 3]  211         sta     UART_ADDR+1                             ; set UTABLE address
   114F 20 A9 13      [ 6]  212         jsr     AGCUPD
   1152 20 ED 13      [ 6]  213         jsr     KUPDATE
   1155 20 D3 12      [ 6]  214         jsr     UARTPROC
   1158 AD 02 01      [ 4]  215         lda     UART_02
   115B 29 05         [ 2]  216         and     #0x05
   115D F0 23         [ 4]  217         beq     $46
   115F A5 67         [ 3]  218         lda     UART_RBYTE
   1161 D0 0C         [ 4]  219         bne     $45
   1163 AD 01 01      [ 4]  220         lda     UART_01
   1166 C9 53         [ 2]  221         cmp     #'S                                     ; 'S' - start command?
   1168 D0 18         [ 4]  222         bne     $46
   116A E6 67         [ 5]  223         inc     UART_RBYTE
   116C 4C 82 11      [ 3]  224         jmp     $46
   116F                     225 $45:
   116F A9 00         [ 2]  226         lda     #0x00
   1171 85 67         [ 3]  227         sta     UART_RBYTE
   1173 AD 01 01      [ 4]  228         lda     UART_01
   1176 C9 31         [ 2]  229         cmp     #'1                                     ; '1' - 2nd byte startplay command?
   1178 F0 36         [ 4]  230         beq     STARTPLAY
   117A C9 32         [ 2]  231         cmp     #'2                                     ; '2' - 2nd byte lights command?
   117C F0 0A         [ 4]  232         beq     $47
   117E C9 33         [ 2]  233         cmp     #'3                                     ; '3' - 2nd byte lights command?
   1180 F0 1B         [ 4]  234         beq     $48
   1182                     235 $46:
   1182 4C 47 11      [ 3]  236         jmp     WAITPLAY
   1185 4C CA 10      [ 3]  237         jmp     REWIND
                            238 ; lights to all ones
   1188                     239 $47:
   1188 A9 FF         [ 2]  240         lda     #0xFF
   118A 85 98         [ 3]  241         sta     board_7_periph$ddr_reg_a
   118C 85 9A         [ 3]  242         sta     board_7_periph$ddr_reg_b
   118E 85 9C         [ 3]  243         sta     board_8_periph$ddr_reg_a
   1190 85 9E         [ 3]  244         sta     board_8_periph$ddr_reg_b
   1192 8D 02 02      [ 4]  245         sta     U18_PORTB
   1195 A9 02         [ 2]  246         lda     #0x02
   1197 8D 80 02      [ 4]  247         sta     U19_PORTA
   119A 4C 47 11      [ 3]  248         jmp     WAITPLAY
                            249 ; lights to all zeros
   119D                     250 $48:
   119D A9 00         [ 2]  251         lda     #0x00
   119F 85 98         [ 3]  252         sta     board_7_periph$ddr_reg_a
   11A1 85 9A         [ 3]  253         sta     board_7_periph$ddr_reg_b
   11A3 85 9C         [ 3]  254         sta     board_8_periph$ddr_reg_a
   11A5 85 9E         [ 3]  255         sta     board_8_periph$ddr_reg_b
   11A7 8D 02 02      [ 4]  256         sta     U18_PORTB
   11AA 8D 80 02      [ 4]  257         sta     U19_PORTA
   11AD 4C 47 11      [ 3]  258         jmp     WAITPLAY
                            259 
                            260 ;   we have been started!
   11B0                     261 STARTPLAY:
   11B0 20 FB 11      [ 6]  262         jsr     INITBRDS
   11B3 A9 5C         [ 2]  263         lda     #<UTABLE_M1
   11B5 85 69         [ 3]  264         sta     UART_ADDR
   11B7 A9 13         [ 2]  265         lda     #>UTABLE_M1
   11B9 85 6A         [ 3]  266         sta     UART_ADDR+1                             ; set UTABLE address
   11BB A9 00         [ 2]  267         lda     #0x00
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

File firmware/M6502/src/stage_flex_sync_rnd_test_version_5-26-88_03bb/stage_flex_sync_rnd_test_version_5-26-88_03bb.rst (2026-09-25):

                              1 
                              2         .area   region1 (ABS)
                              3 
                              4 ;
                              5 ;       Pizza Time Theatre
                              6 ;       Main Stage Program
                              7 ;       Version Unknown
                              8 ;
                              9 ;       This image was recovered from an unmarked 2732
                             10 ;
                             11 
                     0030    12 RAM_30   = 0x0030
                     0031    13 RAM_31   = 0x0031
                     0032    14 RAM_32   = 0x0032
                     0033    15 RAM_33   = 0x0033
                             16 
                             17 ; Table Addresses go here
                     0034    18 RAM_34   = 0x0034           ; board 2 table address
                     0035    19 RAM_35   = 0x0035           ;   (2 bytes)
                     0036    20 RAM_36   = 0x0036           ; board 5 table address
                     0037    21 RAM_37   = 0x0037           ;   (2 bytes)
                     0038    22 RAM_38   = 0x0038           ; board 1 table address
                     0039    23 RAM_39   = 0x0039           ;   (2 bytes)
                     003A    24 RAM_3A   = 0x003A           ; board 4 table address
                     003B    25 RAM_3B   = 0x003B           ;   (2 bytes)
                     003C    26 RAM_3C   = 0x003C           ; board 3 table address
                     003D    27 RAM_3D   = 0x003D           ;   (2 bytes)
                             28 
                             29 ; IRQ timer section 1
                     003E    30 RAM_3E   = 0x003E           ; 0.1s timer
                     003F    31 RAM_3F   = 0x003F           ; 0.1s timer
                     0040    32 RAM_40   = 0x0040           ; 0.1s timer
                     0041    33 RAM_41   = 0x0041           ; 0.1s timer
                     0042    34 RAM_42   = 0x0042           ; 0.1s timer
                             35 
                     0044    36 RAM_44   = 0x0044
                     0045    37 RAM_45   = 0x0045
                     0046    38 RAM_46   = 0x0046
                     0047    39 RAM_47   = 0x0047
                     0048    40 RAM_48   = 0x0048
                     0049    41 RAM_49   = 0x0049
                     004A    42 RAM_4A   = 0x004A
                             43 
                             44 ; IRQ timer section 2
                     004B    45 RAM_4B   = 0x004B           ; 1ms timer
                     004C    46 RAM_4C   = 0x004C           ; 1ms timer
                     004D    47 RAM_4D   = 0x004D           ; 1ms timer
                     004E    48 RAM_4E   = 0x004E           ; 1ms timer, autoload to 100
                     004F    49 RAM_4F   = 0x004F           ; 0.1s timer
                     0050    50 RAM_50   = 0x0050           ; 0.1s timer
                     0051    51 RAM_51   = 0x0051           ; 0.1s timer
                     0052    52 RAM_52   = 0x0052           ; 0.1s timer, autoload to 100
                     0053    53 RAM_53   = 0x0053           ; 10s timer
                             54 
                     0055    55 RAM_55   = 0x0055           ; program number?
                     0056    56 RAM_56   = 0x0056           ; expected program number?
                     0057    57 RAM_57   = 0x0057
                     0058    58 RAM_58   = 0x0058
                     0059    59 RAM_59   = 0x0059
                     005A    60 RAM_5A   = 0x005A
                     005B    61 RAM_5B   = 0x005B
                     005C    62 RAM_5C   = 0x005C
                     005D    63 RAM_5D   = 0x005D
                     005E    64 RAM_5E   = 0x005E           ; agc related
                     005F    65 RAM_5F   = 0x005F
                     0060    66 RAM_60   = 0x0060
                     0061    67 RAM_61   = 0x0061
                     0062    68 RAM_62   = 0x0062
                     0063    69 RAM_63   = 0x0063
                     0064    70 RAM_64   = 0x0064           ; Command byte
                     0065    71 RAM_65   = 0x0065           ; Channel byte
                     0066    72 RAM_66   = 0x0066           ; Two byte address of current memory
                     0067    73 RAM_67   = 0x0067           ;   address to write to cards
                     0068    74 RAM_68   = 0x0068           ; Current Bitmask
                     0069    75 RAM_69   = 0x0069
                     006A    76 RAM_6A   = 0x006A
                     006B    77 RAM_6B   = 0x006B
                     006C    78 RAM_6C   = 0x006C
                     006D    79 RAM_6D   = 0x006D
                             80 
                     0070    81 RAM_70   = 0x0070
                             82 
                             83         .include "../../include/ptt6502.def"
                              1 
                              2 ;
                              3 ; Peripheral Addresses for PTT 6502 system
                              4 ;
                              5 
                     0000     6 RAM_start                       = 0x0000
                              7 
                              8 ; Board Select 1
                     0080     9 board_1_periph$ddr_reg_a        = 0x0080
                     0081    10 board_1_control_reg_a           = 0x0081
                     0082    11 board_1_periph$ddr_reg_b        = 0x0082
                     0083    12 board_1_control_reg_b           = 0x0083
                             13 
                             14 ; Board Select 2
                     0084    15 board_2_periph$ddr_reg_a        = 0x0084
                     0086    16 board_2_periph$ddr_reg_b        = 0x0086
                             17 
                             18 ; Board Select 3
                     0088    19 board_3_periph$ddr_reg_a        = 0x0088
                     008A    20 board_3_periph$ddr_reg_b        = 0x008A
                             21 
                             22 ; Board Select 4
                     008C    23 board_4_periph$ddr_reg_a        = 0x008C
                     008E    24 board_4_periph$ddr_reg_b        = 0x008E
                             25 
                             26 ; Board Select 5
                     0090    27 board_5_periph$ddr_reg_a        = 0x0090
                     0092    28 board_5_periph$ddr_reg_b        = 0x0092
                             29 
                             30 ; Board Select 6
                     0094    31 board_6_periph$ddr_reg_a        = 0x0094
                             32 
                             33 ; Board Select 7
                     0098    34 board_7_periph$ddr_reg_a        = 0x0098
                     009A    35 board_7_periph$ddr_reg_b        = 0x009A
                             36 
                             37 ; Board Select 8
                     009C    38 board_8_periph$ddr_reg_a        = 0x009C
                     009E    39 board_8_periph$ddr_reg_b        = 0x009E
                             40 
                             41 ; UART / Board Select 11
                     0101    42 UART_01                         = 0x0101
                     0102    43 UART_02                         = 0x0102
                             44 
                             45 ; 1st 6532 on CPU board
                     0200    46 U18_PORTA                       = 0x0200
                     0201    47 U18_DDRA                        = 0x0201
                     0202    48 U18_PORTB                       = 0x0202
                     0203    49 U18_DDRB                        = 0x0203
                     0204    50 U18_timer                       = 0x0204
                     0205    51 U18_edge_detect_control_DI_pos  = 0x0205
                     0206    52 U18_06                          = 0x0206    
                     0215    53 U18_timer_8T_DI                 = 0x0215
                     0217    54 U18_17                          = 0x0217
                     021C    55 U18_1C                          = 0x021C    ; timer div by 1, enable interrupt
                     021D    56 U18_1D                          = 0x021D    ; timer div by 1, disable interrupt
                             57 
                             58 ; 2nd 6532 on CPU board
                     0280    59 U19_PORTA                       = 0x0280
                     0281    60 U19_DDRA                        = 0x0281
                     0282    61 U19_PORTB                       = 0x0282
                     0283    62 U19_DDRB                        = 0x0283
                     0285    63 U19_edge_detect_control_DI_pos  = 0x0285
                     0286    64 U19_06                          = 0x0286
                             65 
                             66 ; XPRT / Board Select 12
                     0300    67 transport_periph$ddr_reg_a      = 0x0300
                     0301    68 transport_control_reg_a         = 0x0301
                     0302    69 transport_periph$ddr_reg_b      = 0x0302
                     0303    70 transport_control_reg_b         = 0x0303
                             71 
                             72 ; AUDIO / Board Select 13
                     0380    73 audio_periph$ddr_reg_a          = 0x0380
                     0381    74 audio_control_reg_a             = 0x0381
                     0382    75 audio_periph$ddr_reg_b          = 0x0382
                     0383    76 audio_control_reg_b             = 0x0383
                             77 
                             78 ; Tape Commands
                     0010    79 TAPEMODE_STOP                   = 0x10
                     0020    80 TAPEMODE_FFWD                   = 0x20
                     0040    81 TAPEMODE_REWIND                 = 0x40
                     0080    82 TAPEMODE_PLAY                   = 0x80
                             83 
                             84 
                             85 
                             86 
                             87 
                             88 
                             84 
   1000                      85         .org    0x1000
                             86 ;
                             87 ;       IRQ handler
                             88 ;
   1000                      89 IRQ:
   1000 48            [ 3]   90         pha
   1001 AD 05 02      [ 4]   91         lda     U18_edge_detect_control_DI_pos          ; clear PA7 flag
   1004 AD 85 02      [ 4]   92         lda     U19_edge_detect_control_DI_pos          ; clear PA7 flag
   1007 A9 7D         [ 2]   93         lda     #0x7D                                   ; expire every 125*8=1000us=1ms
   1009 8D 1D 02      [ 4]   94         sta     U18_1D                                  ; div by 8, enable interrupt
   100C A5 4B         [ 3]   95         lda     RAM_4B                                  ; timer
   100E F0 02         [ 4]   96         beq     L1012
   1010 C6 4B         [ 5]   97         dec     RAM_4B
   1012                      98 L1012:
   1012 A5 4C         [ 3]   99         lda     RAM_4C                                  ; timer
   1014 F0 02         [ 4]  100         beq     L1018
   1016 C6 4C         [ 5]  101         dec     RAM_4C
   1018                     102 L1018:
   1018 A5 4D         [ 3]  103         lda     RAM_4D                                  ; timer
   101A F0 02         [ 4]  104         beq     L101E
   101C C6 4D         [ 5]  105         dec     RAM_4D
   101E                     106 L101E:
   101E C6 4E         [ 5]  107         dec     RAM_4E                                  ; timer
   1020 D0 42         [ 4]  108         bne     L1064
   1022 A9 64         [ 2]  109         lda     #0x64
   1024 85 4E         [ 3]  110         sta     RAM_4E
   1026 A5 4F         [ 3]  111         lda     RAM_4F                                  ; timer
   1028 F0 02         [ 4]  112         beq     L102C
   102A C6 4F         [ 5]  113         dec     RAM_4F
   102C                     114 L102C:
   102C A5 50         [ 3]  115         lda     RAM_50                                  ; timer
   102E F0 02         [ 4]  116         beq     L1032
   1030 C6 50         [ 5]  117         dec     RAM_50
   1032                     118 L1032:
   1032 A5 51         [ 3]  119         lda     RAM_51                                  ; timer
   1034 F0 02         [ 4]  120         beq     L1038
   1036 C6 51         [ 5]  121         dec     RAM_51
   1038                     122 L1038:
   1038 A5 3E         [ 3]  123         lda     RAM_3E                                  ; timer
   103A F0 02         [ 4]  124         beq     L103E
   103C C6 3E         [ 5]  125         dec     RAM_3E
   103E                     126 L103E:
   103E A5 3F         [ 3]  127         lda     RAM_3F                                  ; timer
   1040 F0 02         [ 4]  128         beq     L1044
   1042 C6 3F         [ 5]  129         dec     RAM_3F
   1044                     130 L1044:
   1044 A5 40         [ 3]  131         lda     RAM_40                                  ; timer
   1046 F0 02         [ 4]  132         beq     L104A
   1048 C6 40         [ 5]  133         dec     RAM_40
   104A                     134 L104A:
   104A A5 41         [ 3]  135         lda     RAM_41                                  ; timer
   104C F0 02         [ 4]  136         beq     L1050
   104E C6 41         [ 5]  137         dec     RAM_41
   1050                     138 L1050:
   1050 A5 42         [ 3]  139         lda     RAM_42                                  ; timer
   1052 F0 02         [ 4]  140         beq     L1056
   1054 C6 42         [ 5]  141         dec     RAM_42
   1056                     142 L1056:
   1056 C6 52         [ 5]  143         dec     RAM_52                                  ; timer
   1058 D0 0A         [ 4]  144         bne     L1064
   105A A9 64         [ 2]  145         lda     #0x64
   105C 85 52         [ 3]  146         sta     RAM_52
   105E A5 53         [ 3]  147         lda     RAM_53                                  ; timer
   1060 F0 02         [ 4]  148         beq     L1064
   1062 C6 53         [ 5]  149         dec     RAM_53
   1064                     150 L1064:
   1064 68            [ 4]  151         pla
   1065 40            [ 6]  152         rti
                            153 ;
                            154 ;       Main Program Start
                            155 ;
   1066                     156 RESET:
   1066 D8            [ 2]  157         cld                                             ; No decimal mode
   1067 78            [ 2]  158         sei                                             ; Interrupts are not used
   1068 A2 F0         [ 2]  159         ldx     #0xF0                                   ; Stack is at 0x01F0
   106A 9A            [ 2]  160         txs
   106B A9 00         [ 2]  161         lda     #0x00                                   ; Clear RAM
   106D A2 10         [ 2]  162         ldx     #0x10                                   ; from 0x0010 to 0x007F
   106F                     163 ZERORAM:
   106F 95 00         [ 4]  164         sta     RAM_start,x
   1071 E8            [ 2]  165         inx
   1072 E0 80         [ 2]  166         cpx     #0x80
   1074 D0 F9         [ 4]  167         bne     ZERORAM
   1076 A9 00         [ 2]  168         lda     #0x00                                   ; Initialize these registers to 0x00
   1078 8D 01 03      [ 4]  169         sta     transport_control_reg_a                 ; Clear transport control A, select DDRA
   107B 8D 02 02      [ 4]  170         sta     U18_PORTB                               ; CPU board lights off
   107E 8D 81 03      [ 4]  171         sta     audio_control_reg_a                     ; Clear audio control A, select DDRA
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

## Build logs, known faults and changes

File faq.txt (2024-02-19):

Unofficial Cyberamic Control Center FAQ
Frank Palazzolo
Version: 19 Feb 2024

Disclaimer:

I worked at a Pizza Time Theatre as a high-school student.  Nothing in this document is "official".  The information is based on my own memories, reconstructed by documentation I found on the Internet, and hardware found by myself and other people

System Description:

The Cyberamic Control Center was designed to control the various animatronic stages at Chuck E. Cheese's Pizza Time Theatre.
It's original design was a rack-mounted system, consisting of a Teac reel-to-reel tape deck, a card-cage computer, and various power supplies and audio amplifiers.

Program tapes were distributed on 7-inch reels, which contained mono-audio on one track, and modulated data in the form of audio on the other track.
The control computer had control of the tape deck, so that it could read the audio and data tracks, play the shows from the tape, while generating the control signals to run the animatronics.  Various lighted pushbuttons on the from panel would control the operation of the system.

The data on the tape was ASCII, known as "SongCode" or "Chuck E" format.  The relation between the control codes, the show tracks, and the driver channels is not 100% understood at this time, but it is being worked on.  Some additional data on the tapes was used to allow the system to know, for example, whether a program was Birthday-themed or not.  Because of this, there was a button which could jump to a Birthday program, for example.

Control Computer:

The control computer was modular, consisting of a number of a backplane and a number of cards, so that it could scale to controlling different numbers of channels.
The first three slots were 122-pin, and were reserved for the Transport, Audio Control, and CPU Cards.  The rest of the slots were 50-pin, and were designed for character driver and light driver cards.  All slots had 50-pins in common, while the first 3 slots had extra pins for dedicated functions.

Console:

The Rack-Mounted front panel box contained the various power supplies as well as 8 lighted switches, a power switch, a power indicator, voltage test points, and an AGC knob.  Later variations appear to delete the AGC knob.

Card Descriptions:

- The Orignal CPU card was based on a 1 Mhz, 6502 processor, 2 6532 RIOT chips, and a 4K EPROM containing the firmware.  It could directly access the from panel buttons, and had 8 indicator LEDs.

- The Transport Card contained a 6821 PIA, a UART, and circuitry to decode the data track.  The data was 4800 baud 8N1 serial data, with zero crossings between each bit. The idle state "1" has no mid-bit transition, and "0"s having a mid-bit transition.  It had 6 indicator LEDs.

- The Audio Control Card contained a 6821 PIA, comparators, and analog circuitry including op amps, and DACs.  (At this time, this is not very well understood, but it was reponsible for routing and processing the audio track.  It may also have been possible to override the audio track, as there appears to be background audio and microphone inputs as well.  This card had 7 indicator LEDs.

- The Character and Light Driver cards each contains a 6821 PIA, and were used to switch 24V power to various solenoids or relays, via ribbon connectors on the backs of the cards.  The Character Cards had 14 channels each, while the Light Driver cards have 16 channels.  There were one LED per control channel on these cards.

Firmware:

All of the firmware for the original unit is currently unknown.  This version of the Cyberamic Control Center was used from the earliest rollout of the Pizza Time Theatre until the mid-to-late 1980's. It appears that at least some of controllers for the Caberet stages were never upgraded beyond this original configuration.  This makes sense, because there was little or no new content for those stages after the merger of Pizza Time Theatre and Showbiz.

Discrepencies:

The Audio card seems to have at least two revisions.  Rev A contains an Audio Out amplifier, where Rev C does not.
The Backplane schematics appear to contain a Microphone amplifier, but the drawings don't show a connector.  Further, the backplane schematics show a J19 Audio Out RCA jack, while at least one revision of the backplane (mine) doesn't have this.

Upgrade to SVHS:

At some point (1988?), the system was upgraded to use SVHS tapes instead of Reel-to-reel tapes.  It appears that the Audio Control care was replaced by a new A/V Control card, which was apparently just a slot #6 character card modified to switch 5V instead of 24V.  This card was used to interface with a new TRIAD A/V switcher.  The Audio data track still went to the existing Transport card.  I believe the low level format of the audio data must not have changed, since the same hardware was used to decode it.  It may be that a certain firmware upgrade was needed to support this configuration, but maybe not?

Upgrade to new 68HC11 CPU

Later, in 1993, the system was upgraded again to include an LCD display, and a new CPU card based on a 68HC11 chip.  The functionality of the original Transport card and the A/V Control card were also up-integrated into the new system, so only an adapter card was needed in the Transport slot.  Fortunately, version 1.6 is Cyberstar firmware is available and has been analyzed.  It contains some diagnostics for the system, as well as protocol handlers for at least two variants of the data protocol, R12 and CNR.

Upgrade to DVD? Floppy?:

Later variations of the system used DVDs and Floppy disks to run.  I have very little information about this.

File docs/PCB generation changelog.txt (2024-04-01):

PTT cards changelog

audio

	audio board 0003 rev c
		baseline based on what we have now
		
	audio board 0033 rev a
		added mux controlled by CA2/CB2
		added mux-ed audio out
		removed two of the individual AGC'd but not muxed channels
		amps from previous revision used for muxed output channel
		the logo got rotated and moved
		
character

	Character board 0004 rev.a
		baseline based on what we have now
		
	Character board 0004 rev.b
		shrank the length to the standard dimension
			in doing so the logo got rotated
		
	Character board 0034 rev.a
		removed analog mux section from the 0004 rev.b board
		resistor network became separate resistors
		12v and -12v capacitor locations still exist, as well as test points
		newer smaller square logo
	
	Character board 0034 rev.d
		modern style board (~1993)
		removed all unused chip positions
		switched jumper block to dip switch with warning
		changed to fuse holder instead of solder fuse
		added 24v/5v jumpers for outputs (a/v switcher function)
		went to SIP resistor pack to consolidate things
		removed all 12v and -12v parts and test points
		new silk screen logo
		may have changed the ref des, not on the silk
		
	Character board 0034 rev.e
		24v/5v jumpers now have a default link setting for 24v
		new multi-footprint capacitors
		slight unexplained layout changes
		change of ref des confirmed on the silk 
		
light

	Light board 0021 rev.a
		based off of Character board 0004 rev.b
		removes analog components, but reserves two of the footprints for spare spots, one with power
		removes all 12v and -12v components including test points
		two extra bits for a total of 16
		extra bits use two unused gates of the 7406, not another uln2003a
		has the 50 pin connector for lights, not the character connector
		removed spare sockets and relocated components

	Light board 0021 rev.f
		based off of Character board 0034 rev.e
		no jumpers for output voltage, only 24v
		two extra bits for a total of 16
		extra bits use two unused gates of the 7406, not another uln2003a
		has the 50 pin connector for lights, not the character connector
		
transport
	
	Transport board 0020 rev.a (speculation)
		the baseline for this series of boards is rev.b but the 1982 paper schematic has some clues
		U8 was probably a nand gate for sending serial data out
			this was potentially going to be 9600 baud, but it seems to always have been 4800 in production
		
	Transport board 0020 rev.b
		removed data out nand gate
		otherwise baseline for this series
		
	Transport board 0020 rev.d
		added AH5012 to attenuate incoming data during fast forward and rewind
		this was backported to at least one older transport audio card rev.b
		
cpu

	CPU board 0001 rev.a
		the baseline for this series of boards
		The schematic has inconsistencies with the copper layer on the board
			Two connections have to be made with jumpers (my version adds them in the copper and notes it in silkscreen)
			One connection looks like it was pulled up (mine keeps the via but not the trace)
			The ground net is not fully connected (I didn't change this, it should still work on the backplane that joins it)
			Some pins the schematic claims are grounded are not, no effect on performance
	
	CPU board 0001 rev.b
		This fixes the two jumpers and one cut track from rev.a
		ground problems not fixed
		C3 changed from 10v to 16v, maybe because the 16v ones are cheaper at this point
		everything else seems to be the same
		
	CPU board 0001 rev.c
		only the label calling it rev.c changed
		I did not see any trace changes
		
	CPU board 0001 rev.d
		cut connections to alternate power supplies
		made U20/U22 inoperable
		Made U21 remap to a 2732

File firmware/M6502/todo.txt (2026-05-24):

Todo:

X add more linux disassemblies:
    Add vectors
    Make Table labels start with X
    Add ptt6502 stuff

AAA
X Switch 6 windows builds to linux
    X fixup names
X Fixup all bin commits

BBB
x Rearrange with src dir
x check ptt defs across all assemblies

x need to resolve fill 0xff vs 0x00
x move build script to tools
x create build all 

-------

start fixing up labels/comments?
update front page readme?

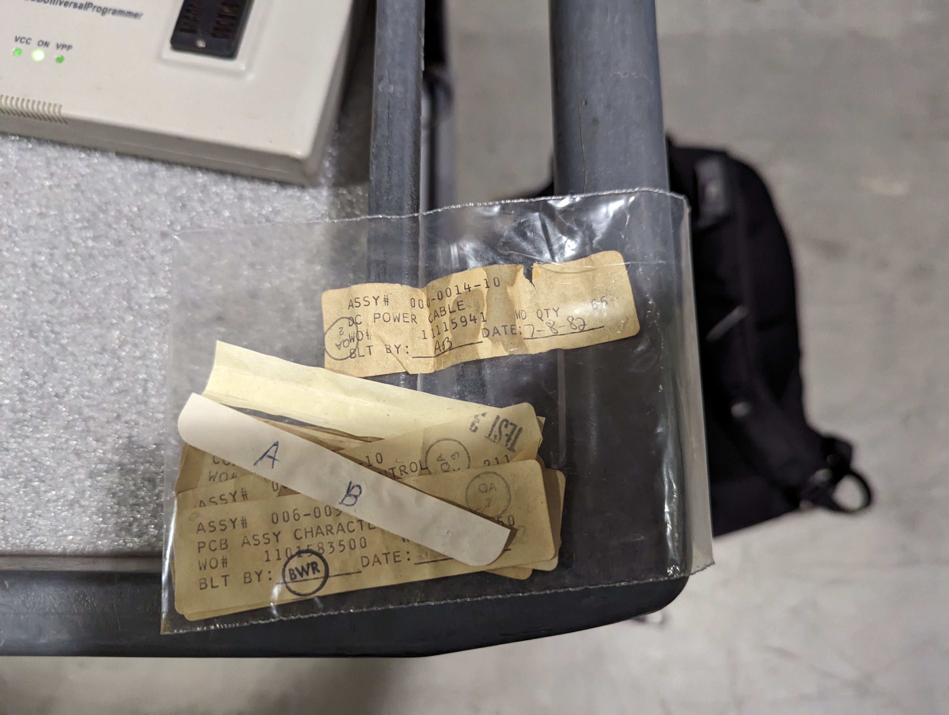
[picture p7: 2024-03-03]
pictures/History San Jose - Half a Chuck/PXL_20240226_182802124.RAW-01.COVER.jpg

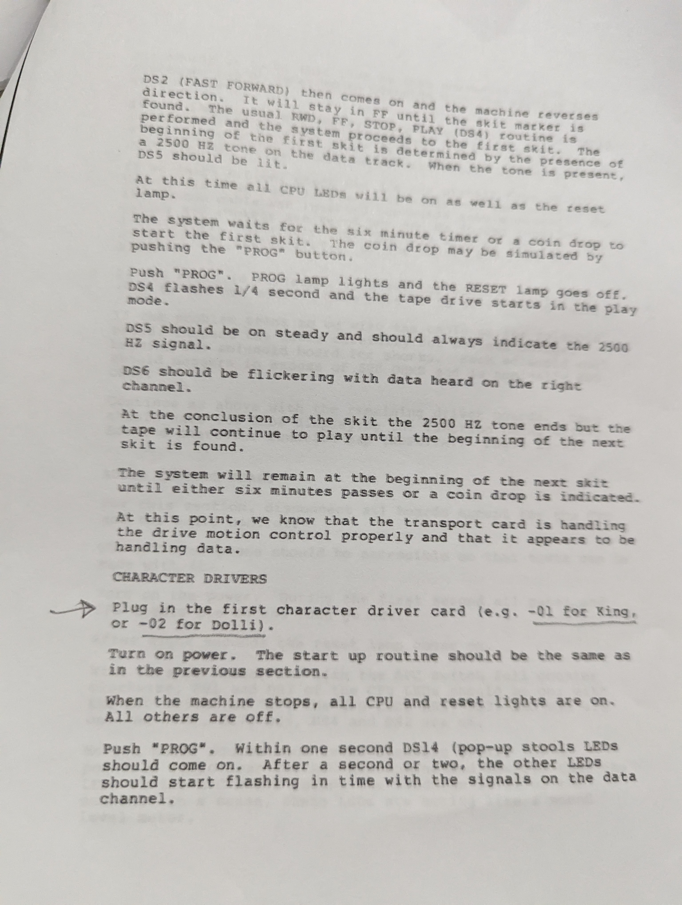
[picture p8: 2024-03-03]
pictures/History San Jose - Half a Chuck/PXL_20240226_192202579.RAW-01.COVER.jpg

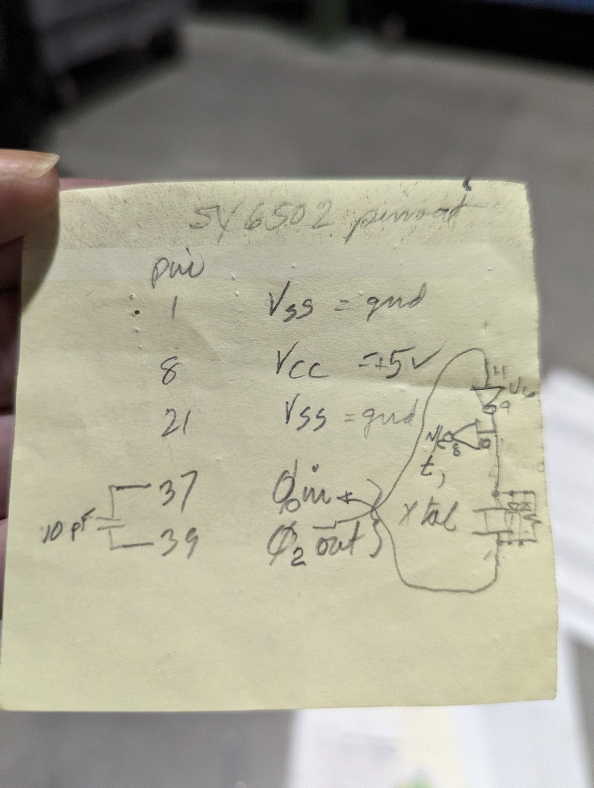
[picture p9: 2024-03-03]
pictures/History San Jose - Half a Chuck/PXL_20240226_191714379.RAW-01.COVER.jpg

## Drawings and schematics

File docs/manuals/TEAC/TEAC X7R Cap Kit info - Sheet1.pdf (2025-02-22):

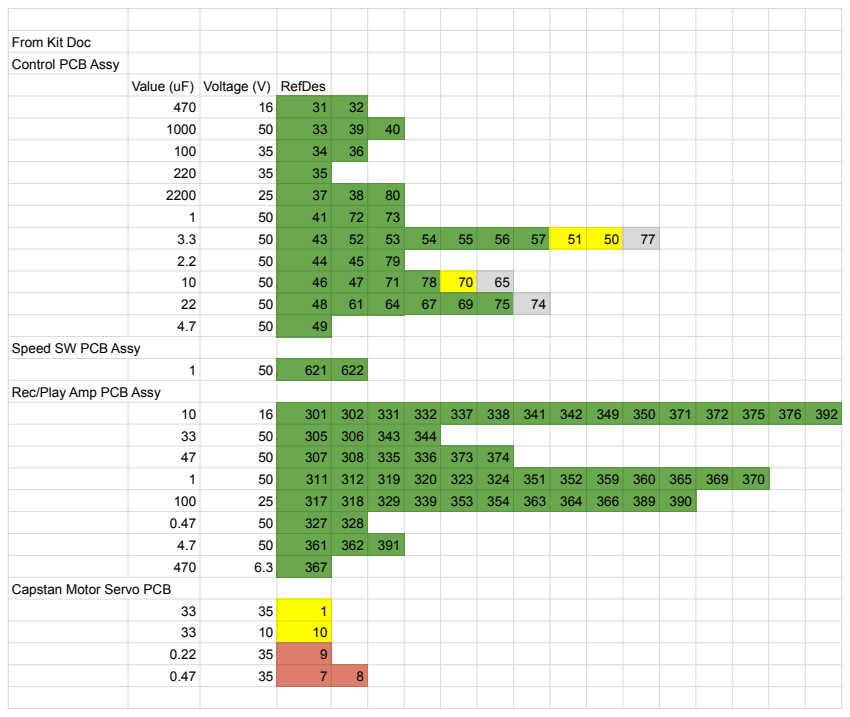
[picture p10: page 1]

From Kit Doc
Control PCB Assy

Value (uF) Voltage (V) RefDes

Speed SW PCB Assy

Rec/Play Amp PCB Assy

Capstan Motor Servo PCB

Key
| Replaced, on BOM from kit
| Replaced, not on BOM from kit
| Not replaced, not on BOM from kit
| on BOM from kit, no part on X7/X7R

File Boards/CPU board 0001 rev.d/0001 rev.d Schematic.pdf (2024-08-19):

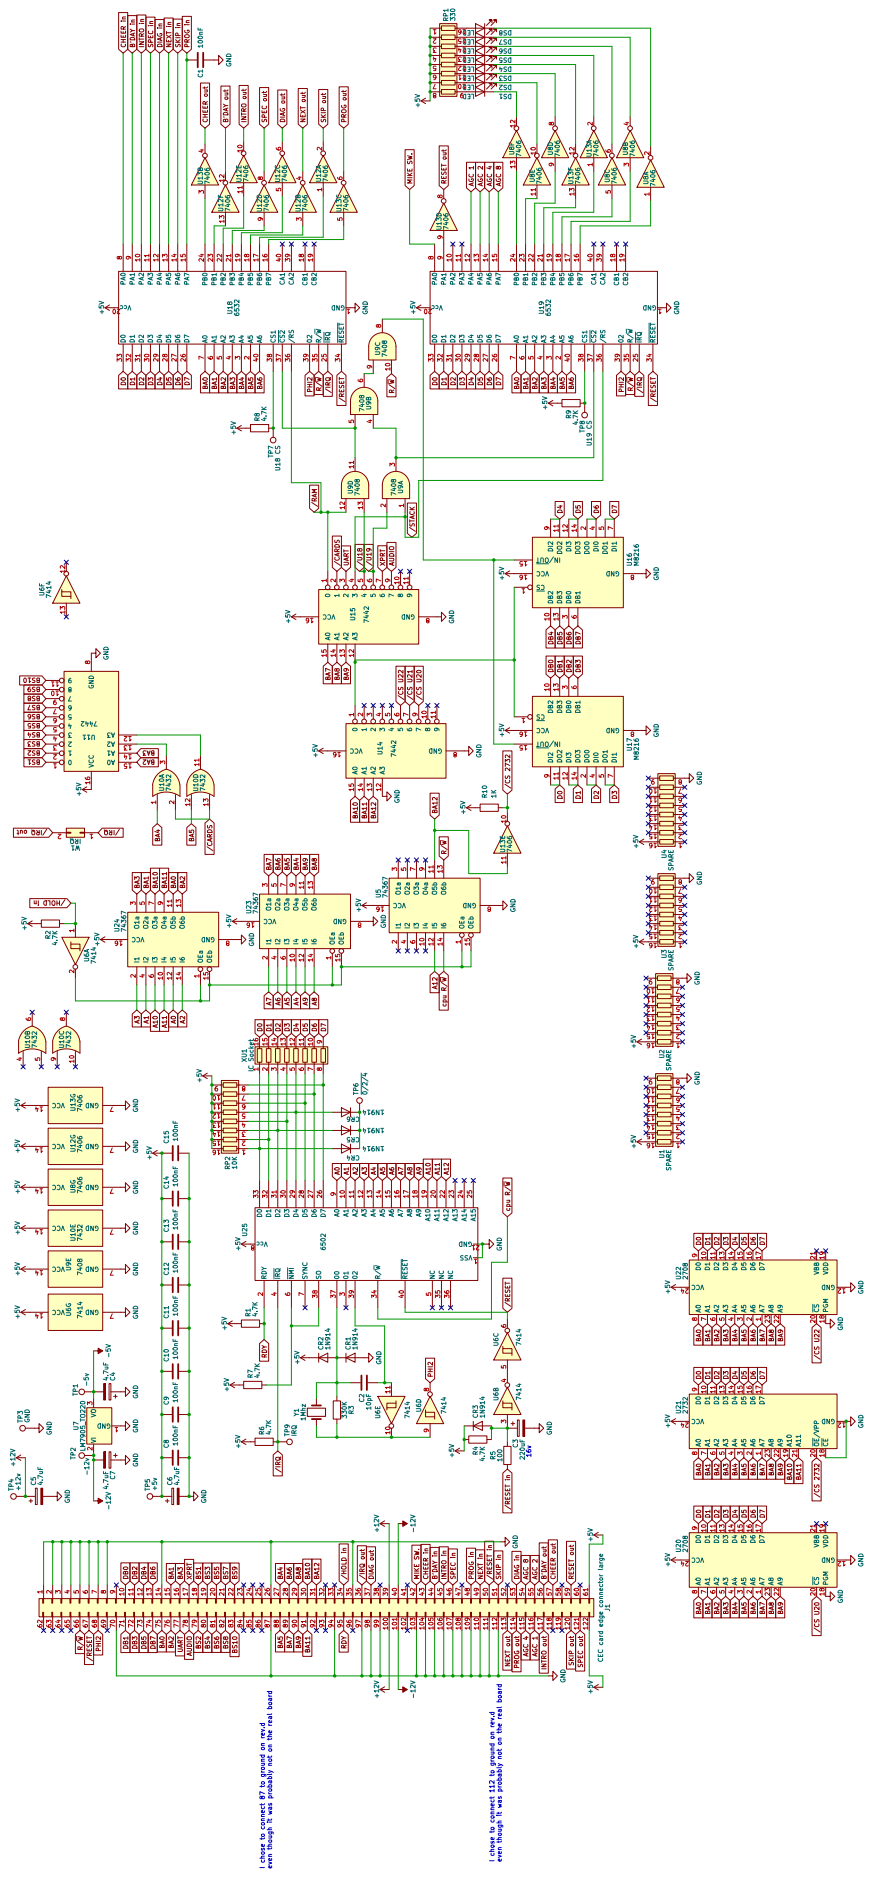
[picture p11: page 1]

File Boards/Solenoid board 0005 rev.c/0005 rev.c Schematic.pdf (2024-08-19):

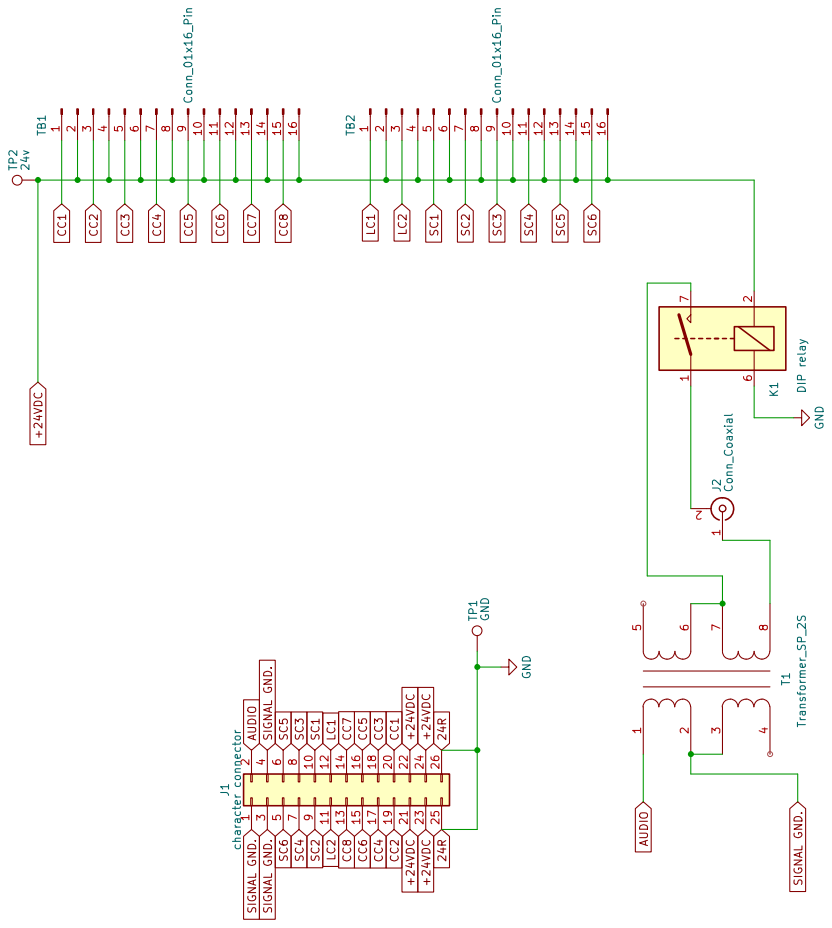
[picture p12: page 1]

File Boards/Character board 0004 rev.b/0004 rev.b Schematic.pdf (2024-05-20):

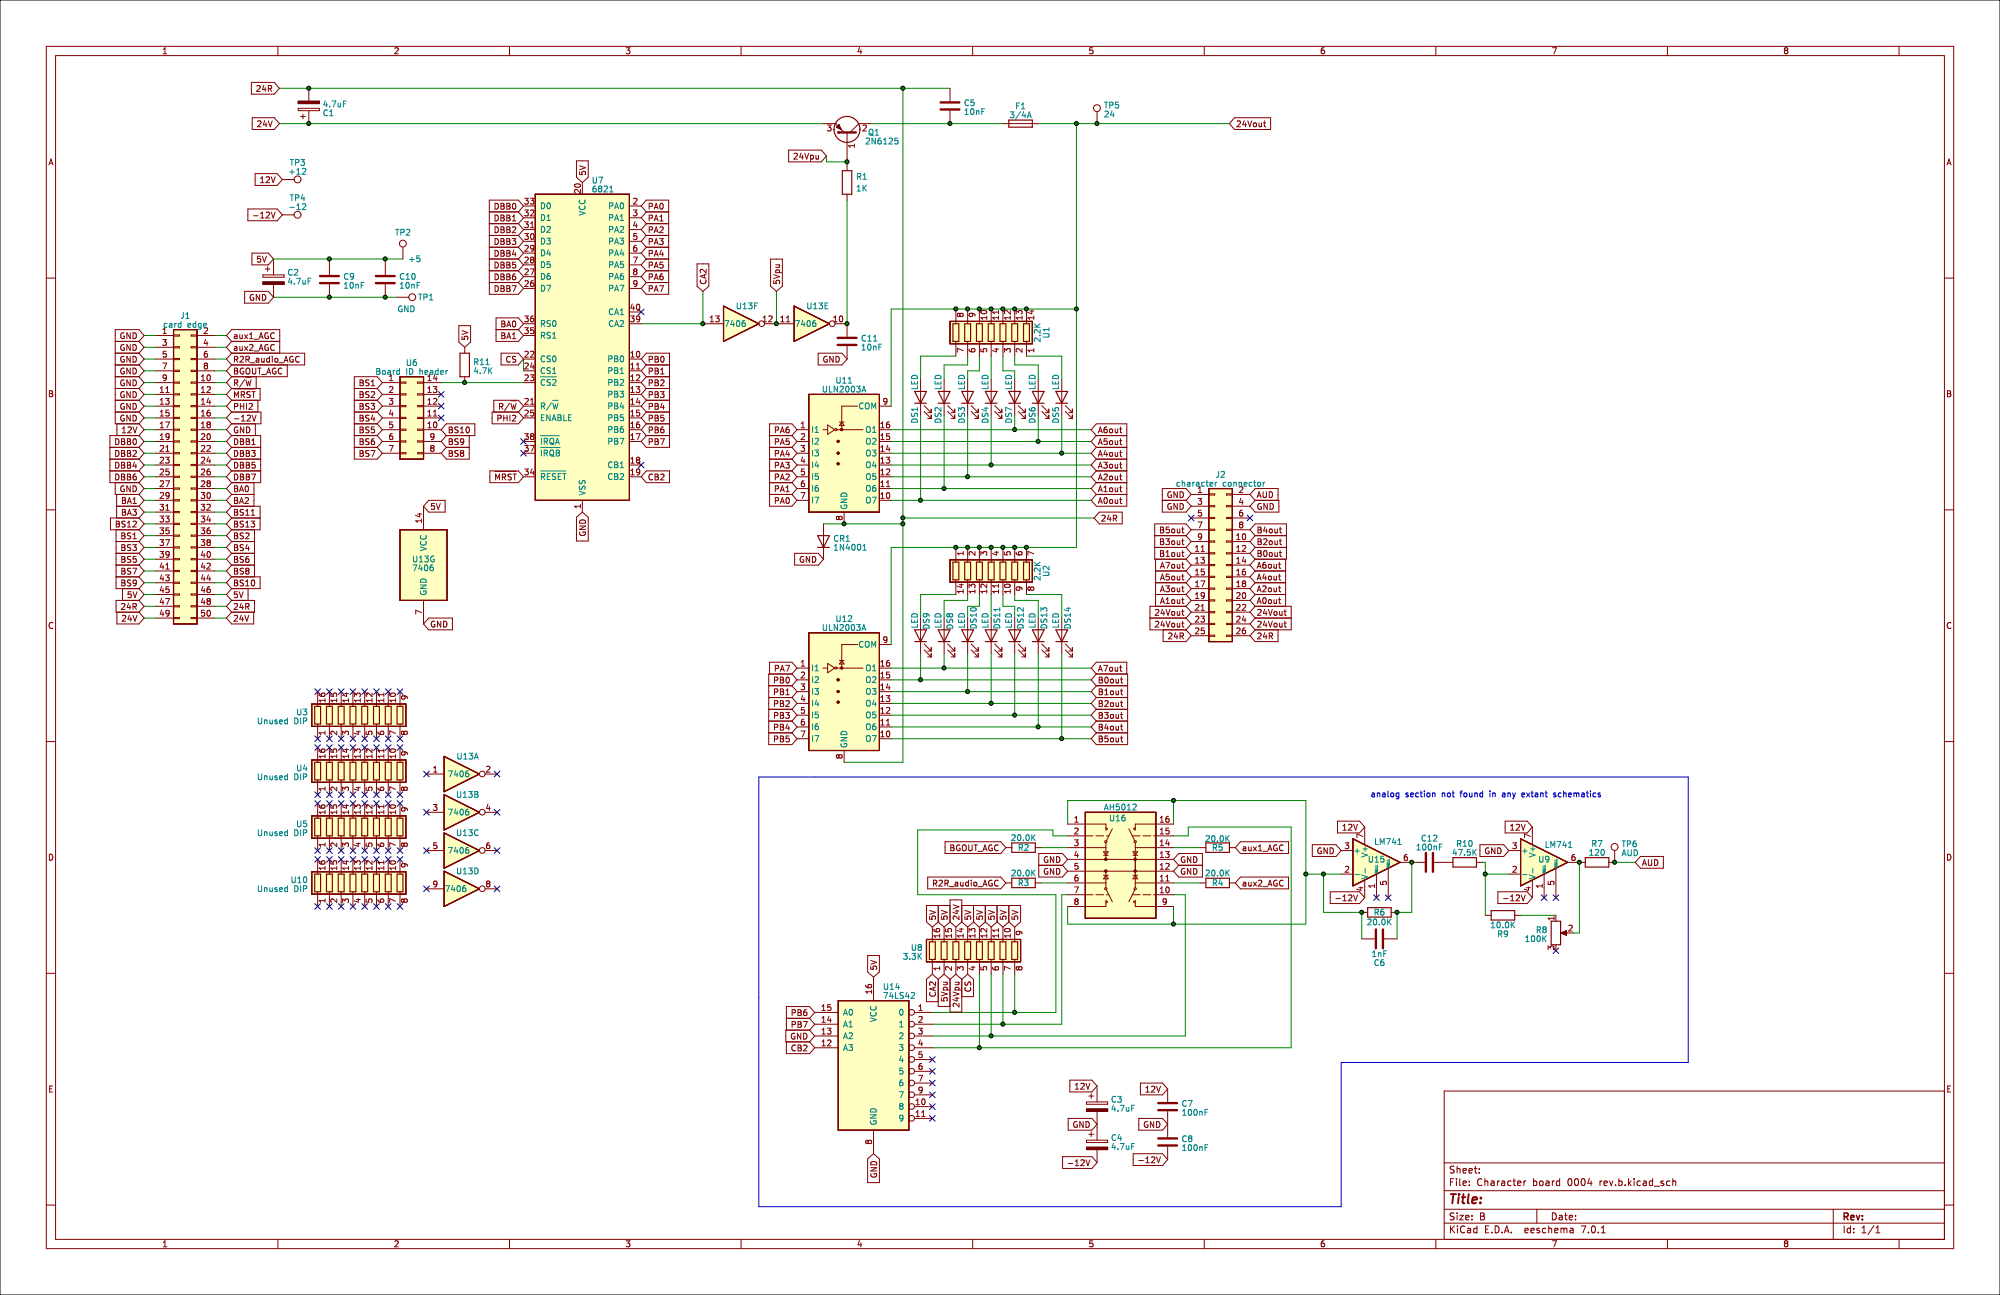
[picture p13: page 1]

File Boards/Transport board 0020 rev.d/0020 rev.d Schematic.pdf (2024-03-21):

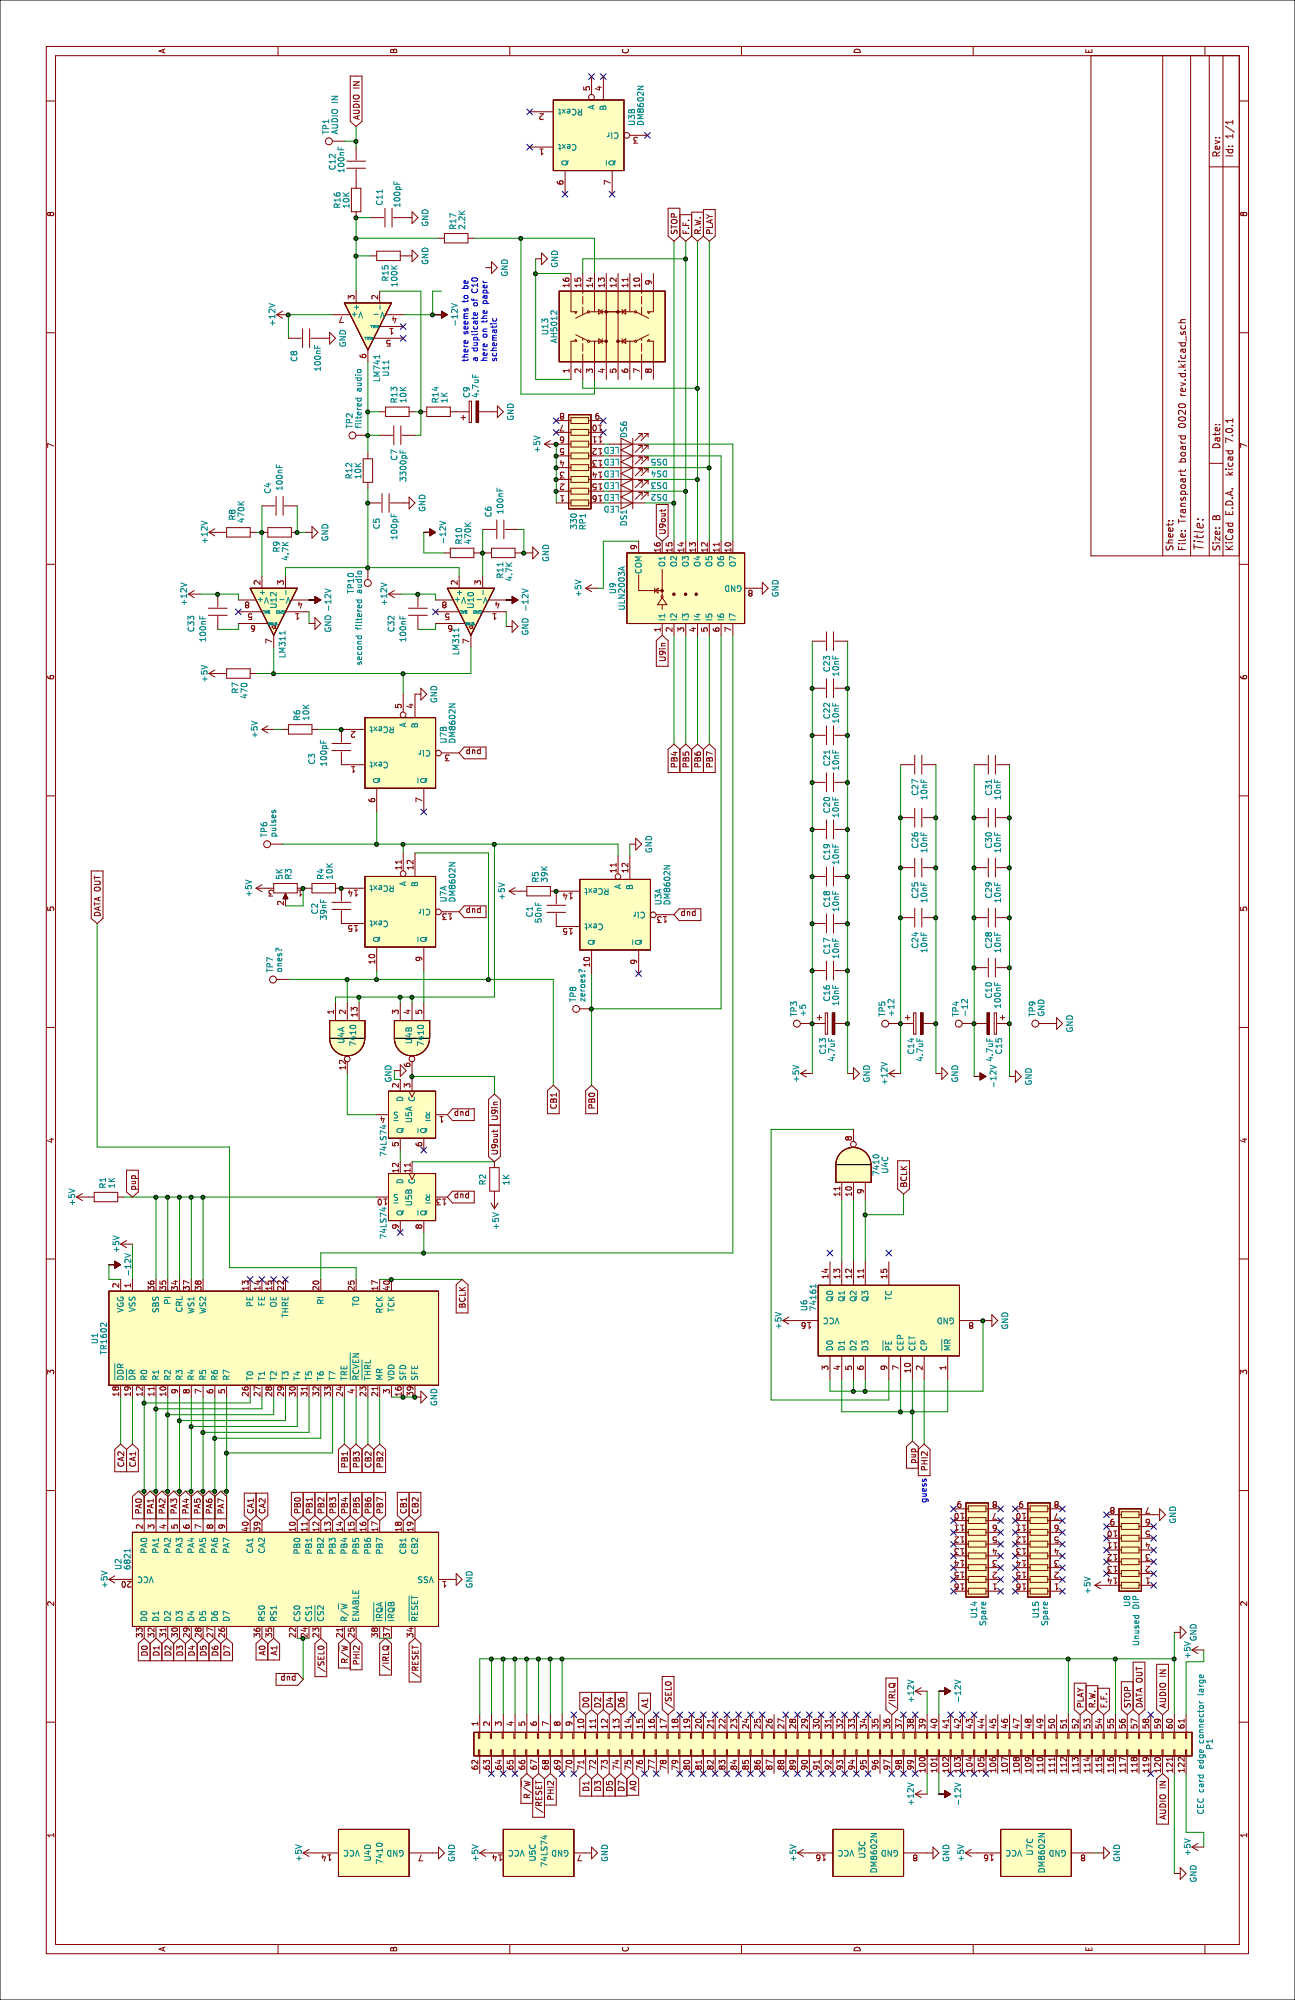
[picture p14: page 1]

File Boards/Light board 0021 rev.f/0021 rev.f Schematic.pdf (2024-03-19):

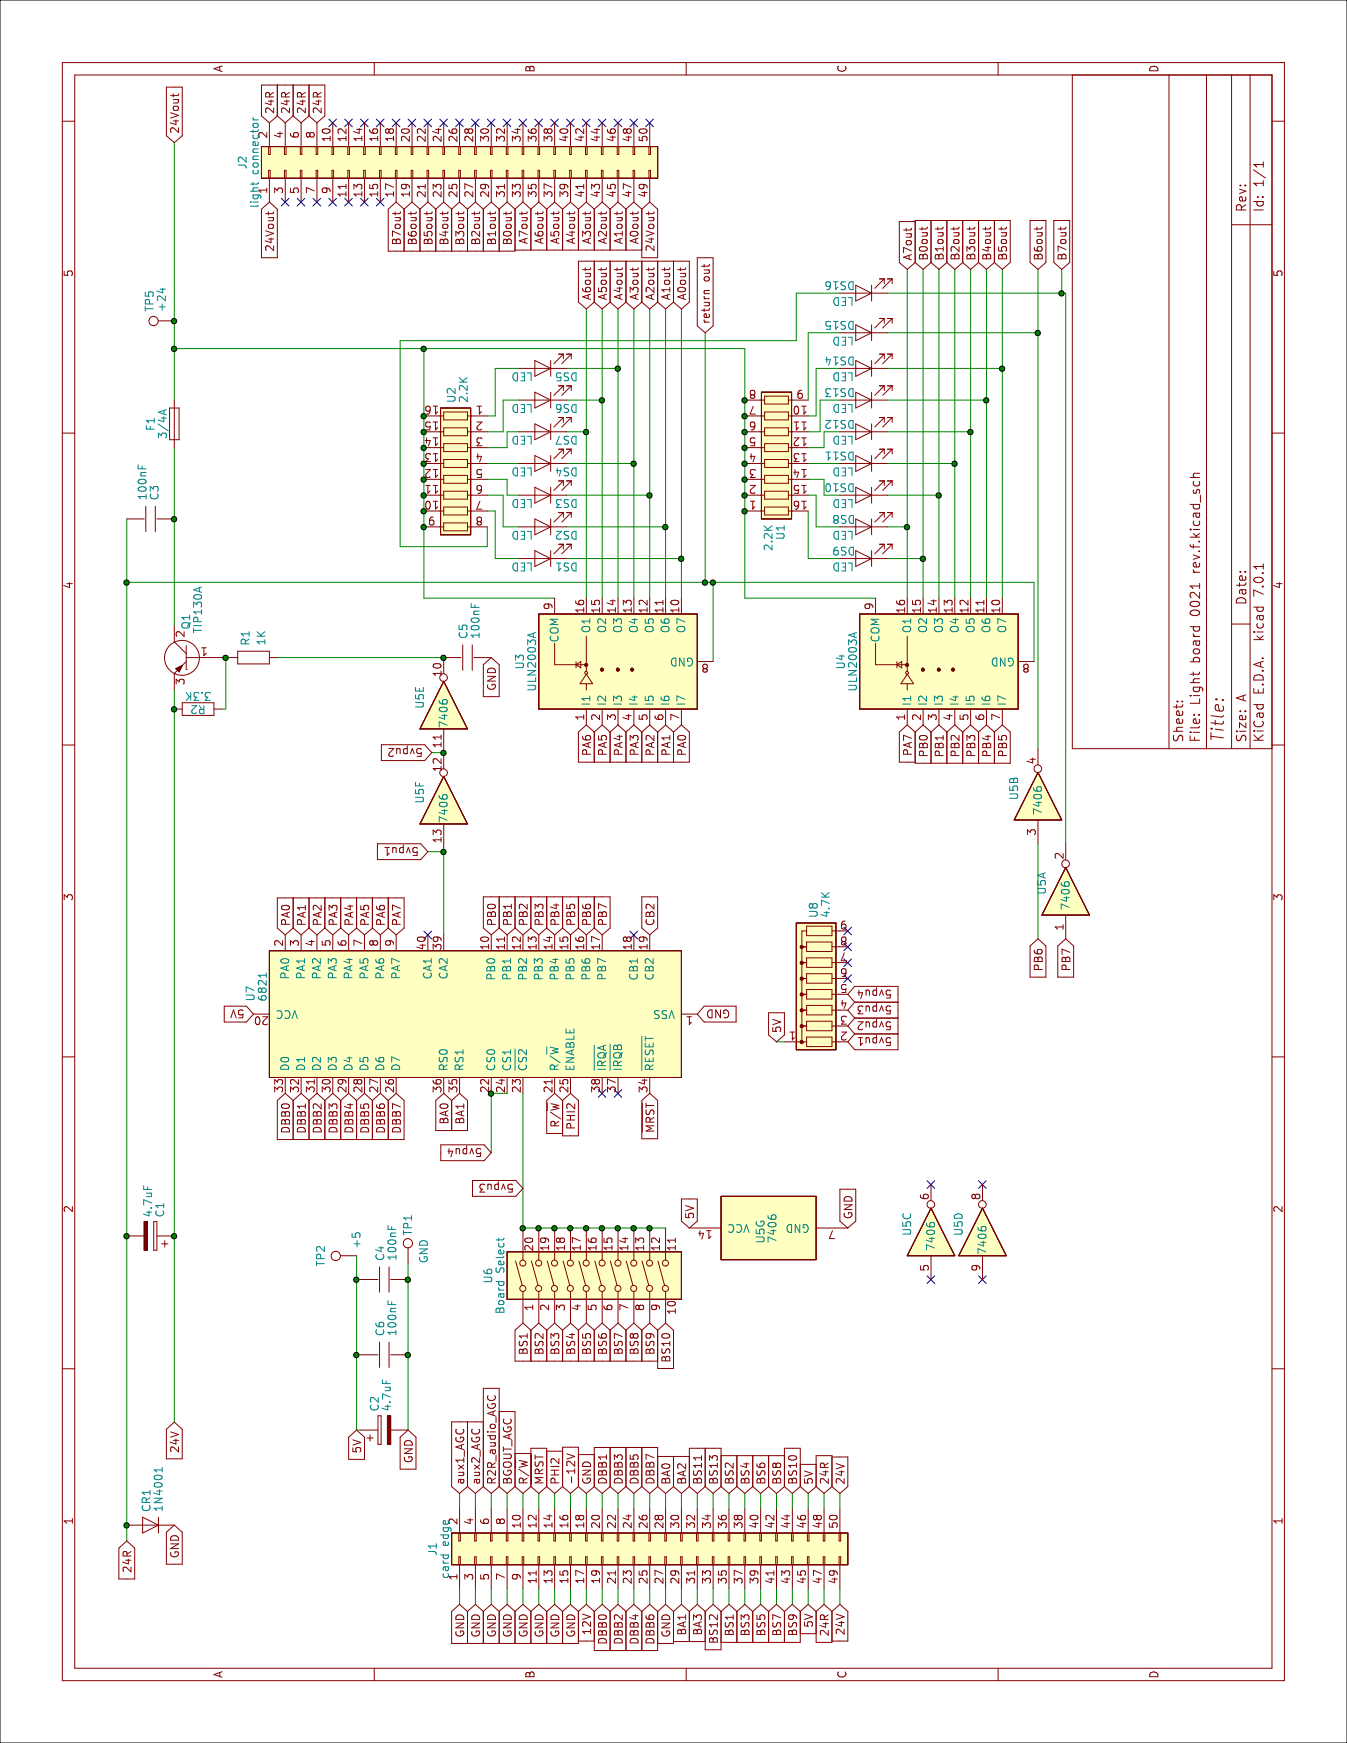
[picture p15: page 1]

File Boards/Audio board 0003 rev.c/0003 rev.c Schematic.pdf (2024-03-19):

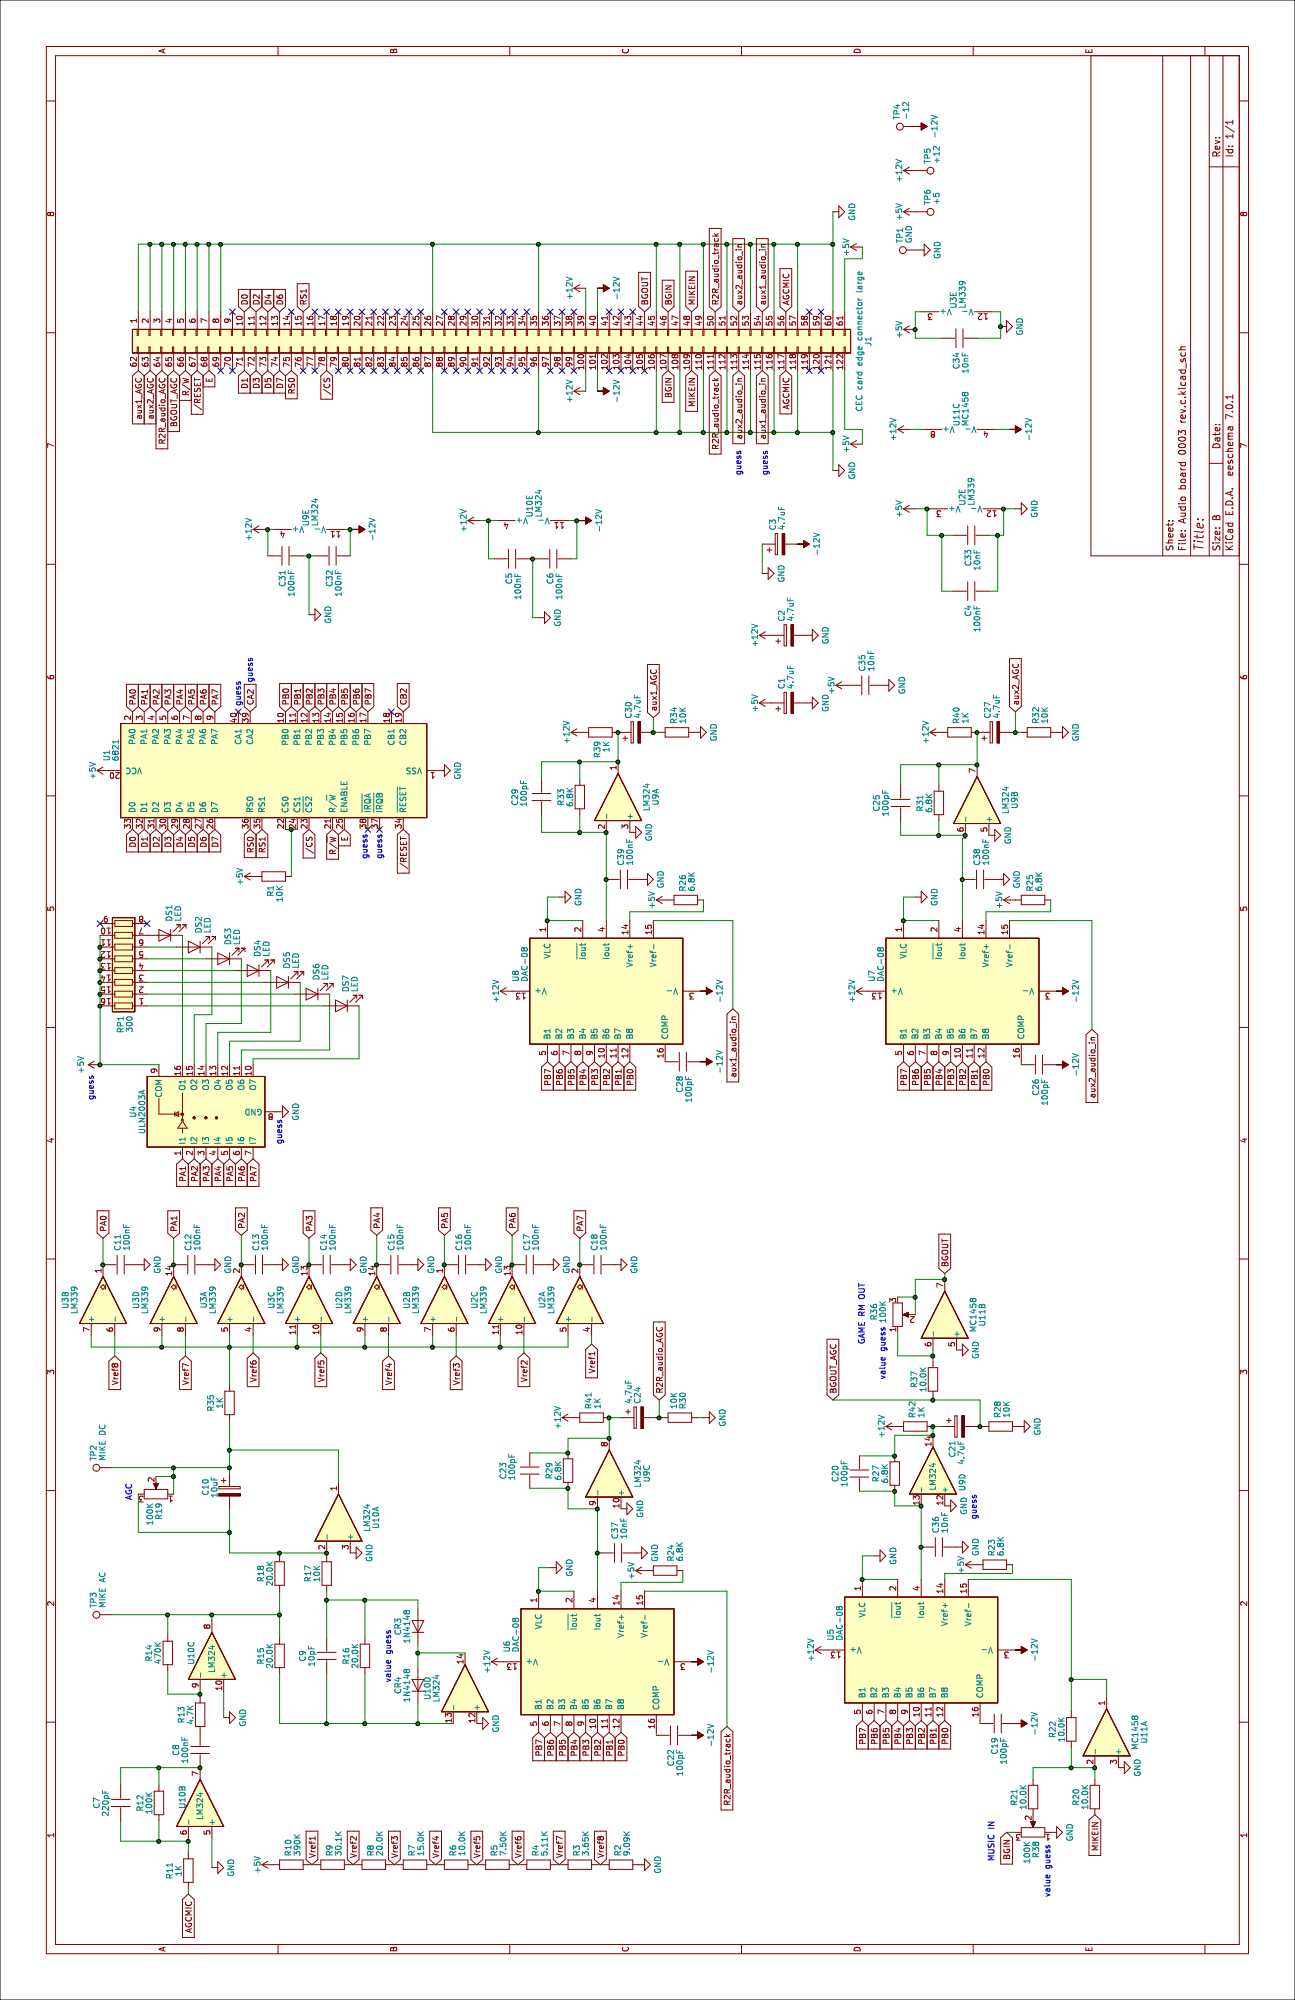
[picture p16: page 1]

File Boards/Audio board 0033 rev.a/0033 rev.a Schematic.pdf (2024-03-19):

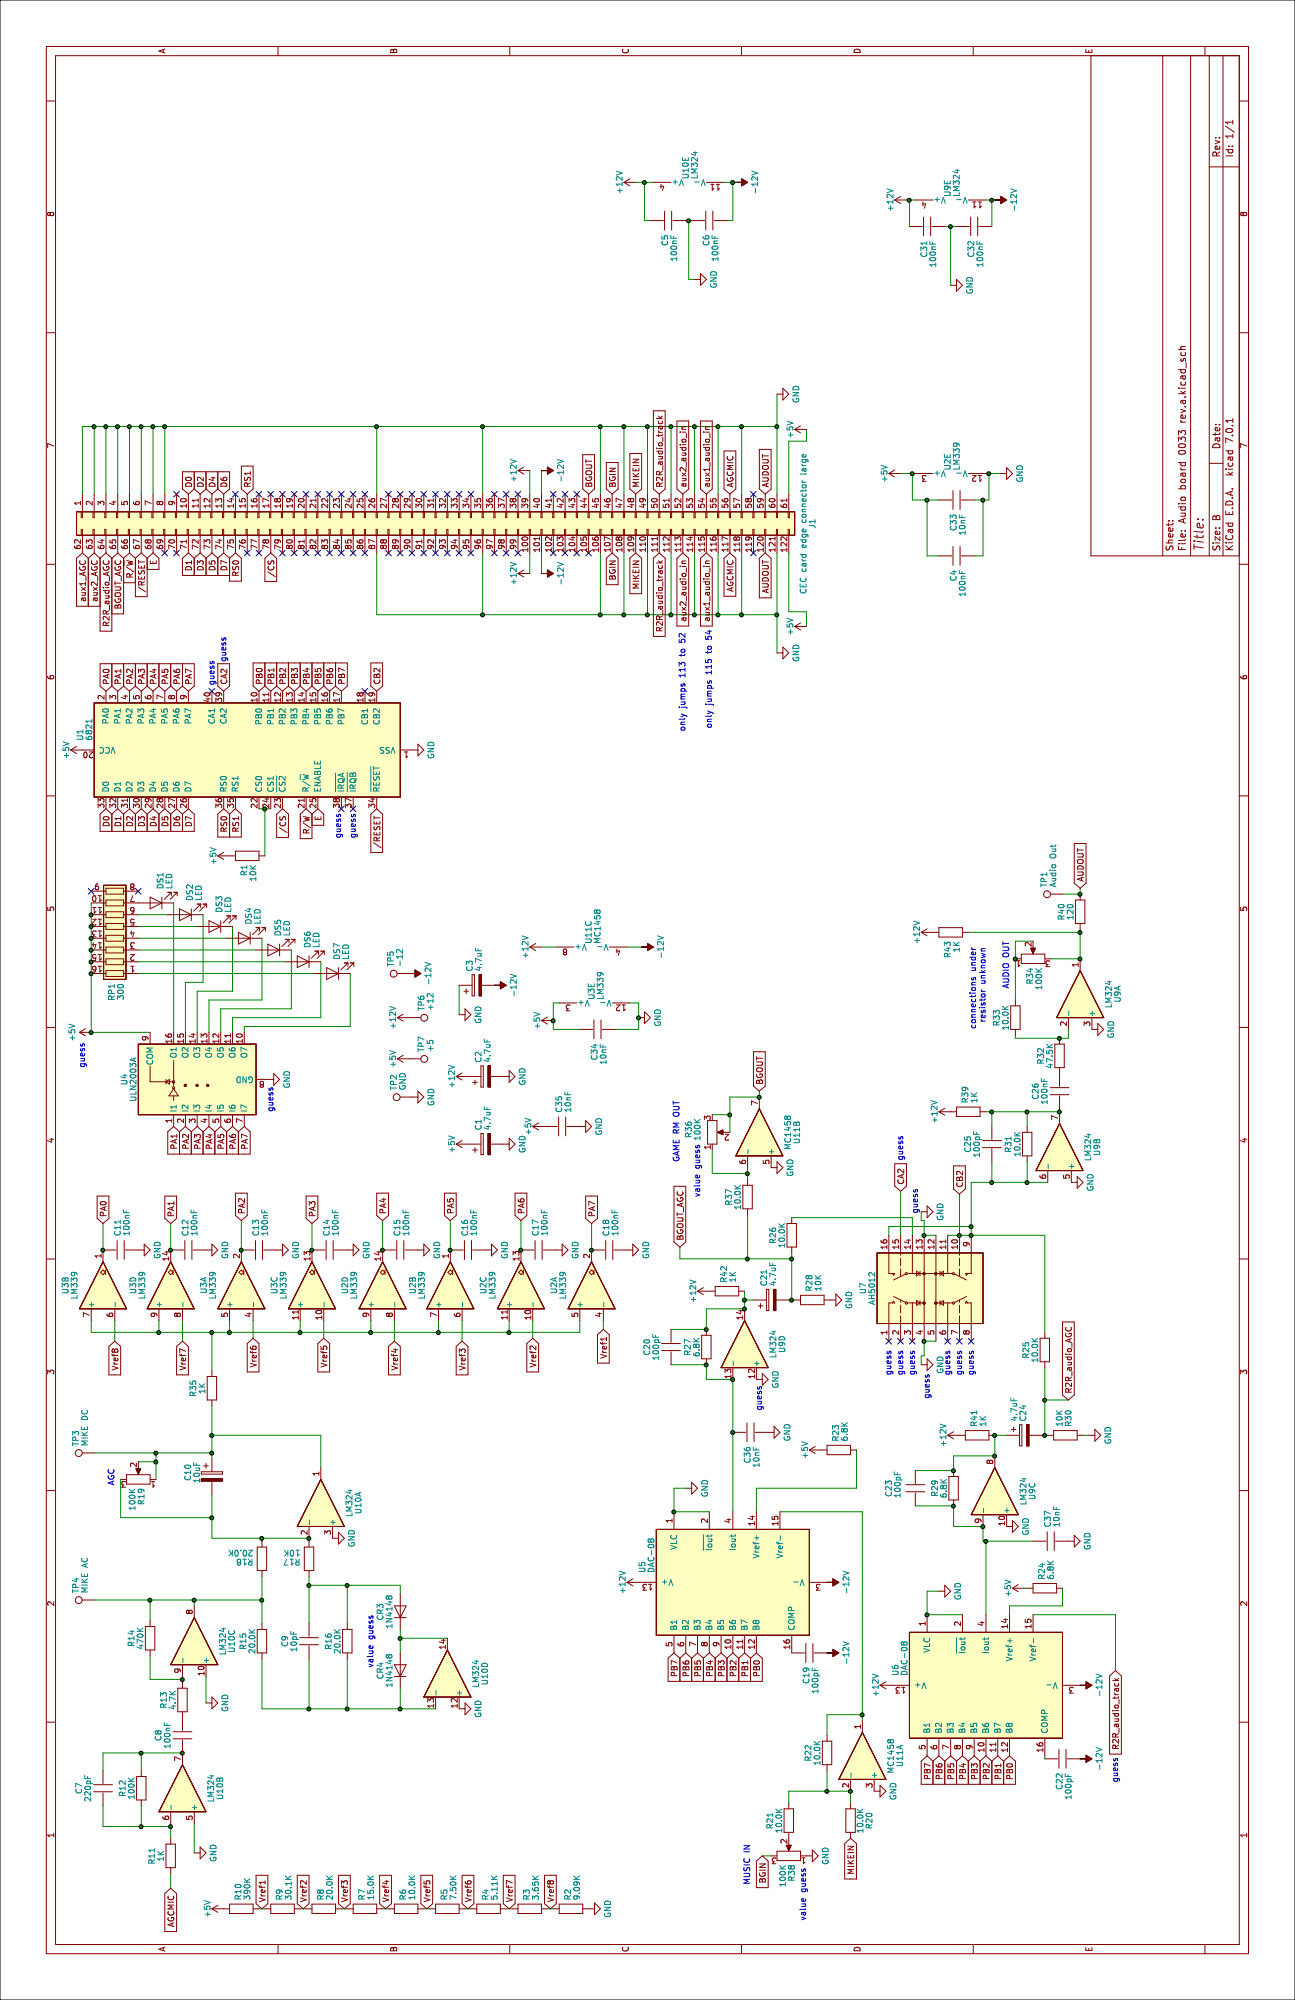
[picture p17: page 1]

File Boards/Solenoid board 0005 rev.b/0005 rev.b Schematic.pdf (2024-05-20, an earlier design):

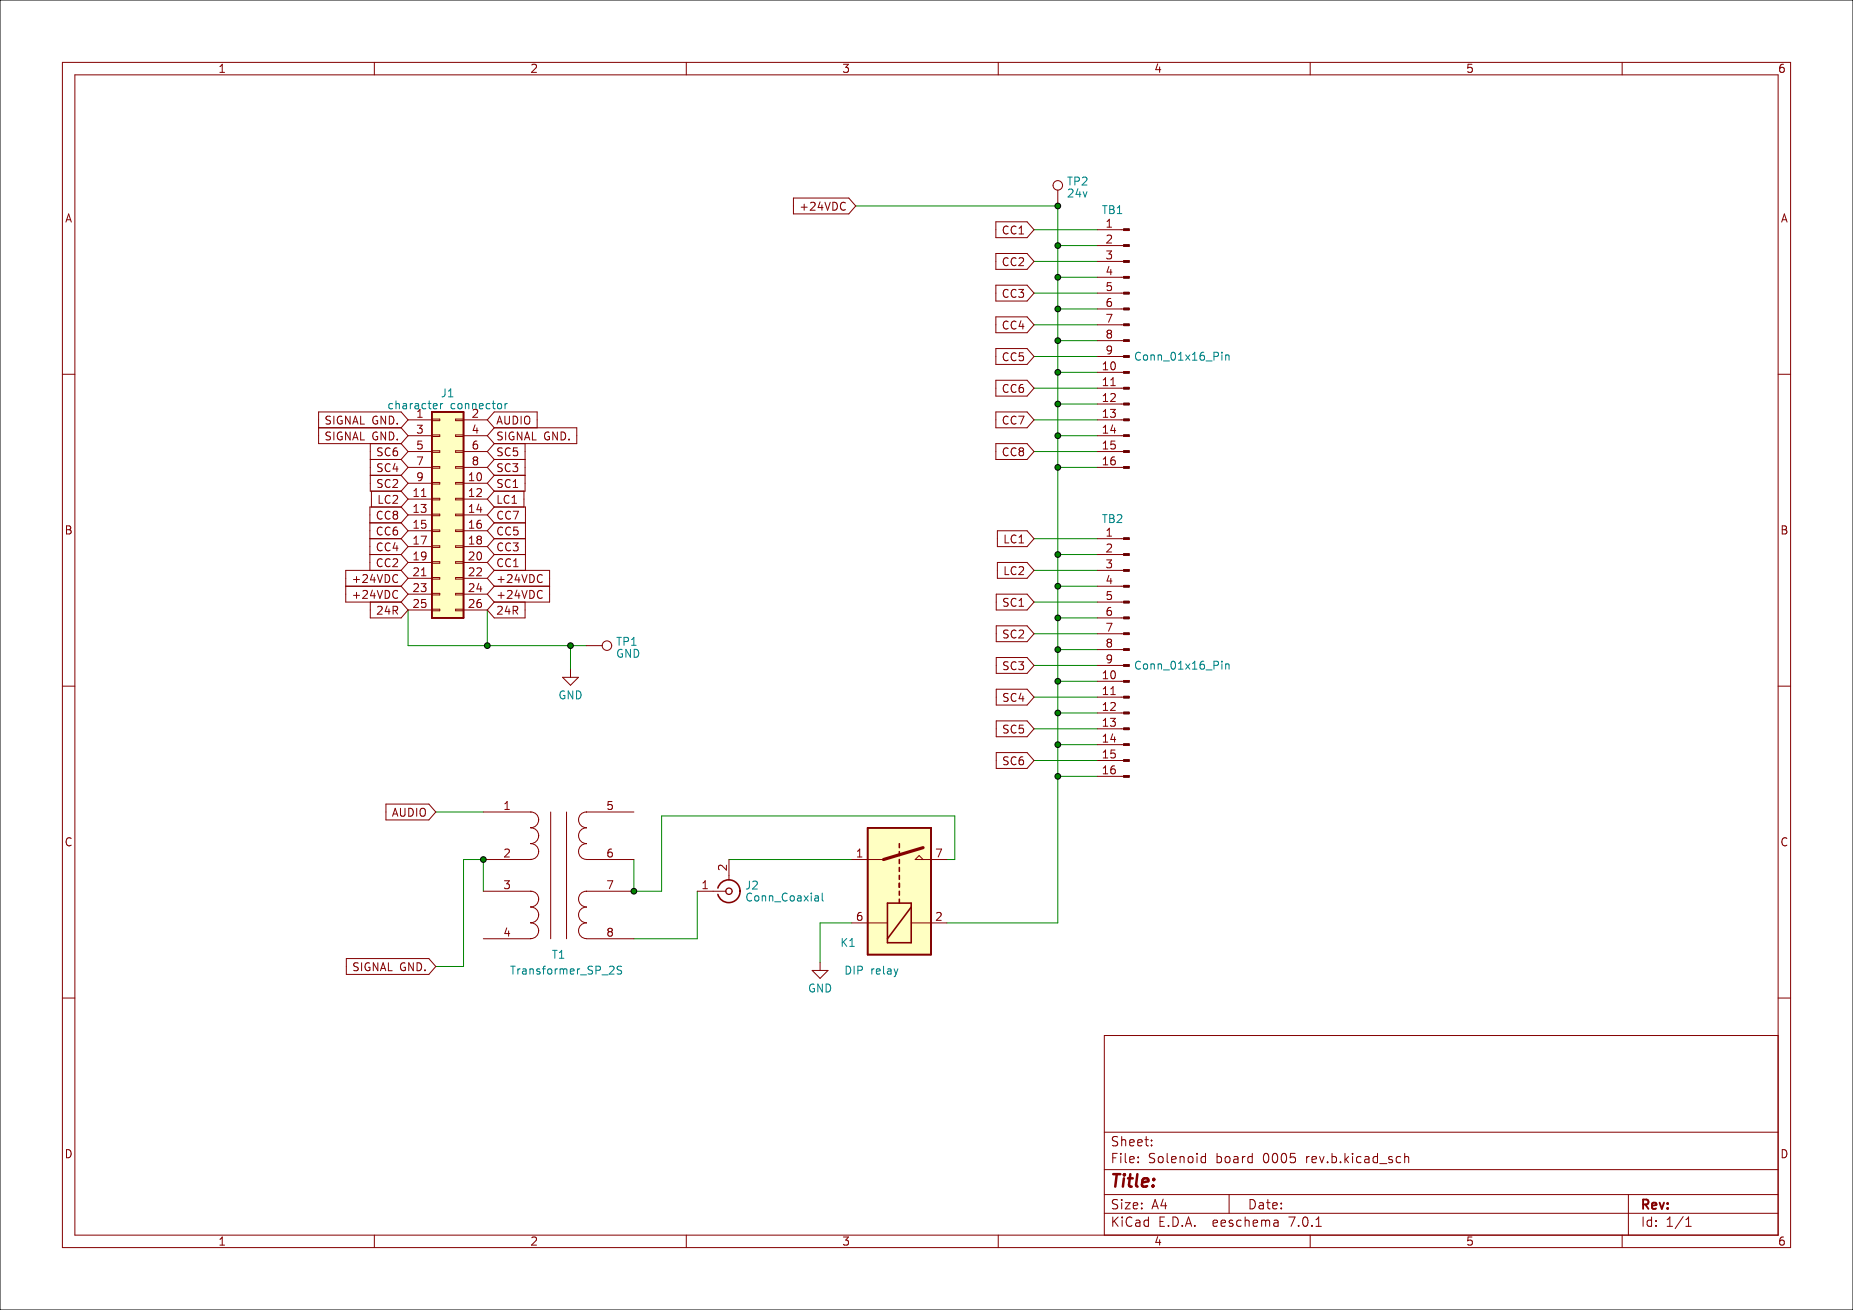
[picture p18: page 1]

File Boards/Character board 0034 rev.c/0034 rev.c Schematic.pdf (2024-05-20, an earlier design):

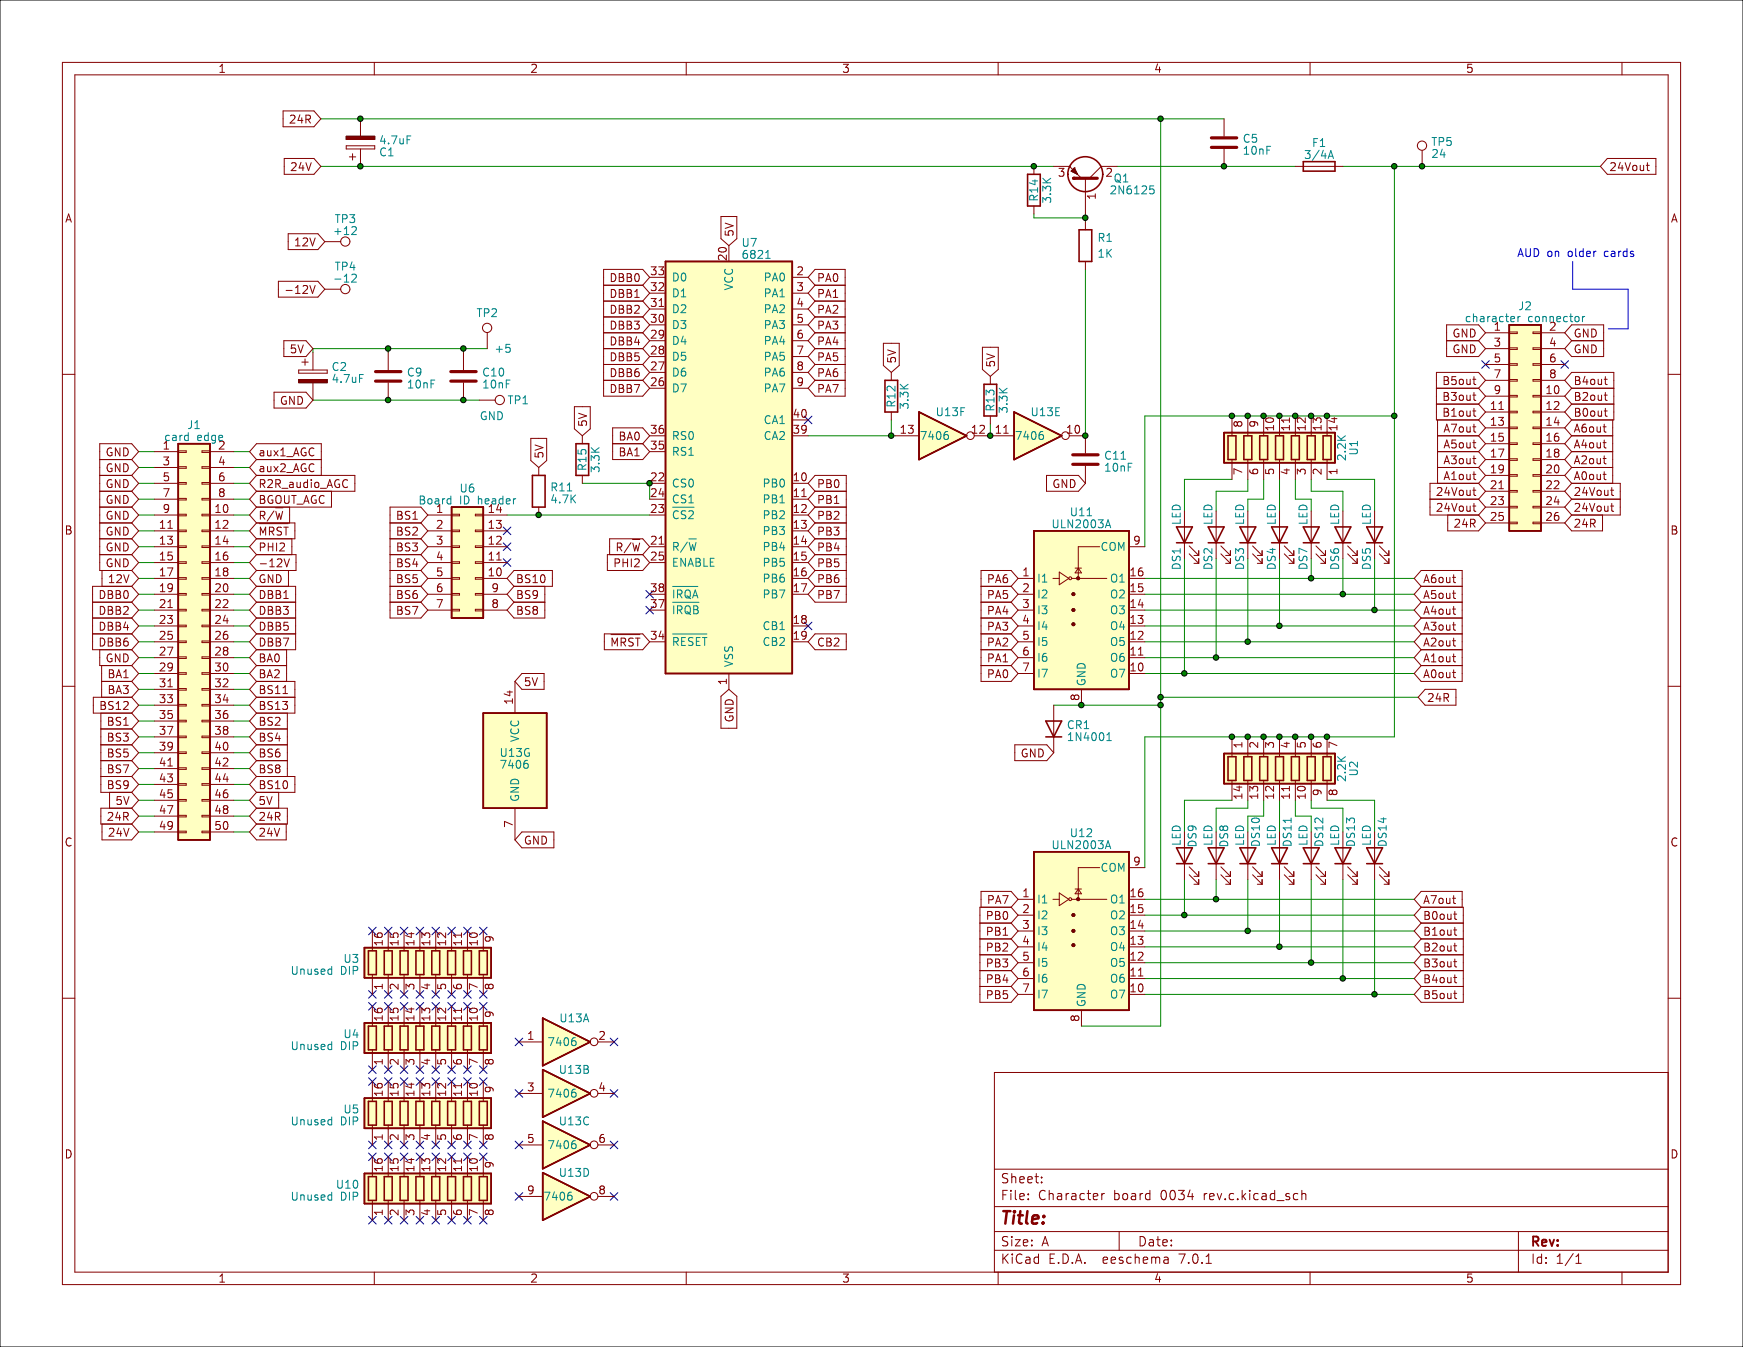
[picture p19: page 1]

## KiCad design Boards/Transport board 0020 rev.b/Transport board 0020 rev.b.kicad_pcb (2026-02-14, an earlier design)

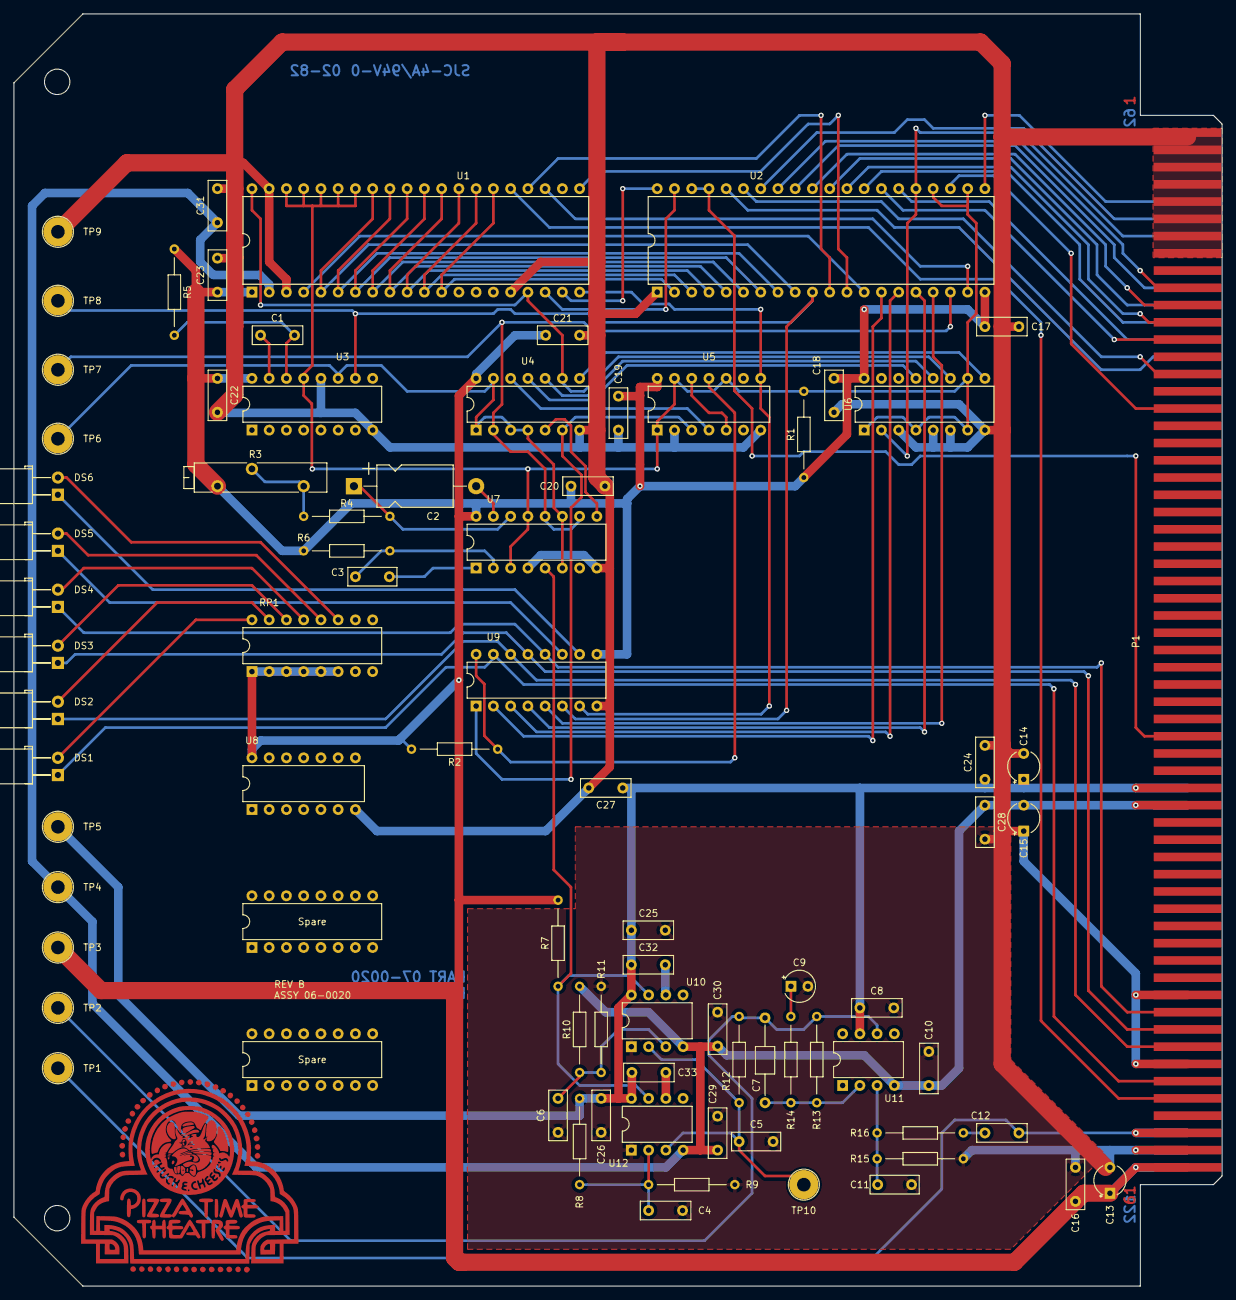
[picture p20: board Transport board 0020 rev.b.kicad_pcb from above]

Board: 2 copper layers, 177.9 x 187.4 mm, 81 parts (0 on the bottom side), 83 nets.

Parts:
C1: 50nF; C_Rect_L7.2mm_W2.5mm_P5.00mm_FKS2_FKP2_MKS2_MKP2
C2: 39nF; CP_Axial_L11.0mm_D6.0mm_P18.00mm_Horizontal
C3, C5, C11: 100pF; C_Rect_L7.0mm_W2.5mm_P5.00mm
C4, C6, C8, C10, C12, C32, C33: 100nF; C_Rect_L7.2mm_W2.5mm_P5.00mm_FKS2_FKP2_MKS2_MKP2
C7: 3300pF; C_Axial_L3.8mm_D2.6mm_P12.50mm_Horizontal
C9: 4.7uF; CP_Radial_Tantal_D4.5mm_P2.50mm
C13, C14, C15: 4.7uF; CP_Radial_Tantal_D4mm_P3.81mm
C16, C17, C18, C19, C20, C21, C22, C23, C24, C25, C26, C27, C28, C29, C30, C31: 10nF; C_Rect_L7.2mm_W2.5mm_P5.00mm_FKS2_FKP2_MKS2_MKP2
DS1, DS2, DS3, DS4, DS5, DS6: LED; LED_D5.0mm_Horizontal_O3.81mm_Z15.0mm reversed
P1: CEC card edge connector large; Chuck_E_Cheese_large_card_edge
R1, R2, R14: 1K; R_Axial_DIN0204_L3.6mm_D1.6mm_P12.7mm_Horizontal
R3: 5K; Potentiometer_Bourns_3005_Horizontal
R4, R6, R12, R13, R16: 10K; R_Axial_DIN0204_L3.6mm_D1.6mm_P12.7mm_Horizontal
R5: 39K; R_Axial_DIN0204_L3.6mm_D1.6mm_P12.7mm_Horizontal
R7: 470; R_Axial_DIN0204_L3.6mm_D1.6mm_P12.7mm_Horizontal
R8, R10: 470K; R_Axial_DIN0204_L3.6mm_D1.6mm_P12.7mm_Horizontal
R9, R11: 4.7K; R_Axial_DIN0204_L3.6mm_D1.6mm_P12.7mm_Horizontal
R15: 100K; R_Axial_DIN0204_L3.6mm_D1.6mm_P12.7mm_Horizontal
RP1: 330; DIP-16_W7.62mm
TP1: AUDIO IN; TestPoint_Plated_Hole_D3.0mm
TP2: filtered audio; TestPoint_Plated_Hole_D3.0mm
TP3: +5; TestPoint_Plated_Hole_D3.0mm
TP4: -12; TestPoint_Plated_Hole_D3.0mm
TP5: +12; TestPoint_Plated_Hole_D3.0mm
TP6: zero crossings; TestPoint_Plated_Hole_D3.0mm
TP7: bits; TestPoint_Plated_Hole_D3.0mm
TP8: carrier detect; TestPoint_Plated_Hole_D3.0mm
TP9: GND; TestPoint_Plated_Hole_D3.0mm
TP10: second filtered audio; TestPoint_Plated_Hole_D3.0mm
U1: TR1602; DIP-40_W15.24mm
U2: 6821; DIP-40_W15.24mm
U3, U7: DM8602N; DIP-16_W7.62mm
U4: 7410; DIP-14_W7.62mm
U5: 74LS74; DIP-14_W7.62mm
U6: 74161; DIP-16_W7.62mm
U8: Unused DIP; DIP-14_W7.62mm
U9: ULN2003A; DIP-16_W7.62mm
U10, U12: LM311; DIP-8_W7.62mm
U11: LM741; DIP-8_W7.62mm
U14, U15: Spare; DIP-16_W7.62mm

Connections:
+5V: C13.1, C16.1, C17.1, C18.1, C19.1, C20.1, C21.1, C22.1, C23.1, P1.61, P1.122, R1.1, R2.2, R3.3, R5.1, R6.1, R7.1, RP1.1 (R1.1), RP1.2 (R2.1), RP1.3 (R3.1), RP1.4 (R4.1), RP1.5 (R5.1), RP1.6 (R6.1), TP3.1, U1.1 (VSS), U2.20 (VCC), U3.16 (VCC), U4.14 (VCC), U5.14 (VCC), U6.16 (VCC), U7.16 (VCC), U8.14 (R1.2), U9.9 (COM)
+12V: C8.1, C14.1, C24.1, C25.1, C26.1, C27.1, C32.2, C33.2, P1.39, P1.100, R8.2, TP5.1, U10.8 (V+), U11.7 (V+), U12.8 (V+)
-12V: C10.1, C15.2, C28.1, C29.1, C30.1, C31.1, P1.40, P1.101, R10.1, TP4.1, U1.2 (VGG), U10.4 (V-), U11.4 (V-), U12.4 (V-)
A0: P1.75, U2.36 (RS0)
A1: P1.15, U2.35 (RS1)
AUDIO IN: C12.1, P1.59, P1.120, TP1.1
BCLK: U1.17 (RCK), U1.40 (TCK), U4.9, U6.11 (Q3)
CA1: U1.19 (~DR), U2.40 (CA1)
CA2: U1.18 (~DDR), U2.39 (CA2)
CB1: TP7.1, U2.18 (CB1), U4.2, U7.10 (Q), U7.12 (B)
CB2: U1.23 (~THRL), U2.19 (CB2)
D0: P1.10, U2.33 (D0)
D1: P1.71, U2.32 (D1)
D2: P1.11, U2.31 (D2)
D3: P1.72, U2.30 (D3)
D4: P1.12, U2.29 (D4)
D5: P1.73, U2.28 (D5)
D6: P1.13, U2.27 (D6)
D7: P1.74, U2.26 (D7)
DATA OUT: P1.57, U1.25 (TO)
F.F.: DS2.1 (K), P1.54, U9.14 (O3)
GND: C4.2, C5.1, C6.2, C8.2, C9.2, C10.2, C11.1, C13.2, C14.2, C15.1, C16.2, C17.2, C18.2, C19.2, C20.2, C21.2, C22.2, C23.2, C24.2, C25.2, C26.2, C27.2, C28.2, C29.2, C30.2, C31.2, P1.1, P1.2, P1.3, P1.4, P1.5, P1.6, P1.7, P1.8, P1.51, P1.55, P1.60, P1.121, R9.2, R11.2, R15.2, TP9.1, U1.3 (VDD), U1.16 (SFD), U1.39 (SFE), U2.1 (VSS), U3.8 (GND), U3.12 (B), U4.7 (GND), U5.2 (D), U5.7 (GND), U6.3 (D0), U6.5 (D2), U6.6 (D3), U6.8 (GND), U7.4 (B), U7.8 (GND), U8.7 (R7.1), U9.8 (GND), U10.1 (GND), U12.1 (GND)
unnamed: C7.2, R12.1, R13.1, TP2.1, U11.6
unnamed: C9.1, R14.2
unnamed: C12.2, R16.1
unnamed: DS1.2 (A), RP1.16 (R1.2)
unnamed: DS2.2 (A), RP1.15 (R2.2)
unnamed: DS3.2 (A), RP1.14 (R3.2)
unnamed: DS4.2 (A), RP1.13 (R4.2)
unnamed: DS5.2 (A), RP1.12 (R5.2)
unnamed: DS5.1 (K), U9.11 (O6)
unnamed: DS6.2 (A), RP1.11 (R6.2)
unnamed: DS6.1 (K), U9.10 (O7)
unnamed: R3.1, R3.2, R4.1
unnamed: U1.20 (RI), U5.8 (~Q), U9.7 (I7)
unnamed: TP6.1, U3.11 (A), U4.1, U4.3, U4.4, U4.13, U7.6 (Q), U7.11 (A)
unnamed: C1.2, U3.15 (Cext)
unnamed: C1.1, R5.2, U3.14 (RCext)
unnamed: U5.5 (Q), U5.12 (D)
unnamed: U4.12, U5.4 (~S)
unnamed: U4.11, U6.13 (Q1)
unnamed: U4.10, U6.12 (Q2)
unnamed: U4.8, U6.9 (~PE)
unnamed: C2.2, U7.15 (Cext)
unnamed: C2.1, R4.2, U7.14 (RCext)
unnamed: U4.5, U7.9 (~Q)
unnamed: R7.2, U7.5 (A), U10.7, U12.7
unnamed: C3.1, U7.1 (Cext)
unnamed: C3.2, R6.2, U7.2 (RCext)
unnamed: C5.2, R12.2, TP10.1, U10.2 (+), U12.3 (-)
unnamed: C6.1, R10.2, R11.1, U10.3 (-)
unnamed: C32.1, U10.6 (STRB)
unnamed: C11.2, R15.1, R16.2, U11.3 (+)
unnamed: C7.1, R13.2, R14.1, U11.2 (-)
unnamed: C4.1, R8.1, R9.1, U12.2 (+)
unnamed: C33.1, U12.6 (STRB)
PA0: U1.12 (R0), U1.26 (T0), U2.2 (PA0)
PA1: U1.11 (R1), U1.27 (T1), U2.3 (PA1)
PA2: U1.10 (R2), U1.28 (T2), U2.4 (PA2)
PA3: U1.9 (R3), U1.29 (T3), U2.5 (PA3)
PA4: U1.8 (R4), U1.30 (T4), U2.6 (PA4)
PA5: U1.7 (R5), U1.31 (T5), U2.7 (PA5)
PA6: U1.6 (R6), U1.32 (T6), U2.8 (PA6)
PA7: U1.5 (R7), U1.33 (T7), U2.9 (PA7)
PB0: TP8.1, U2.10 (PB0), U3.10 (Q), U9.6 (I6)
PB1: U1.24 (TRE), U2.11 (PB1)
PB2: U1.21 (MR), U2.12 (PB2)
PB3: U1.4 (~RCVEN), U2.13 (PB3)
PB4: U2.14 (PB4), U9.2 (I2)
PB5: U2.15 (PB5), U9.3 (I3)
PB6: U2.16 (PB6), U9.4 (I4)
PB7: U2.17 (PB7), U9.5 (I5)
PHI2: P1.68, U2.25 (ENABLE), U6.2 (CP)
PLAY: DS4.1 (K), P1.52, U9.12 (O5)
R.W.: DS3.1 (K), P1.53, U9.13 (O4)
R/~W: P1.66, U2.21 (R/~W)
STOP: DS1.1 (K), P1.56, U9.15 (O2)
U9in: U4.6, U5.3 (C), U9.1 (I1)
U9out: R2.1, U5.11 (C), U9.16 (O1)
pup: R1.2, U1.34 (CRL), U1.35 (PI), U1.36 (SBS), U1.37 (WS1), U1.38 (WS2), U2.22 (CS0), U2.24 (CS1), U3.13 (Clr), U5.1 (~R), U5.10 (~S), U5.13 (~R), U6.1 (~MR), U6.4 (D1), U6.7 (CEP), U6.10 (CET), U7.3 (Clr), U7.13 (Clr)
/IRLQ: P1.36, U2.37 (~IRQB), U2.38 (~IRQA)
/RESET: P1.67, U2.34 (~RESET)
/SEL0: P1.17, U2.23 (~CS2)

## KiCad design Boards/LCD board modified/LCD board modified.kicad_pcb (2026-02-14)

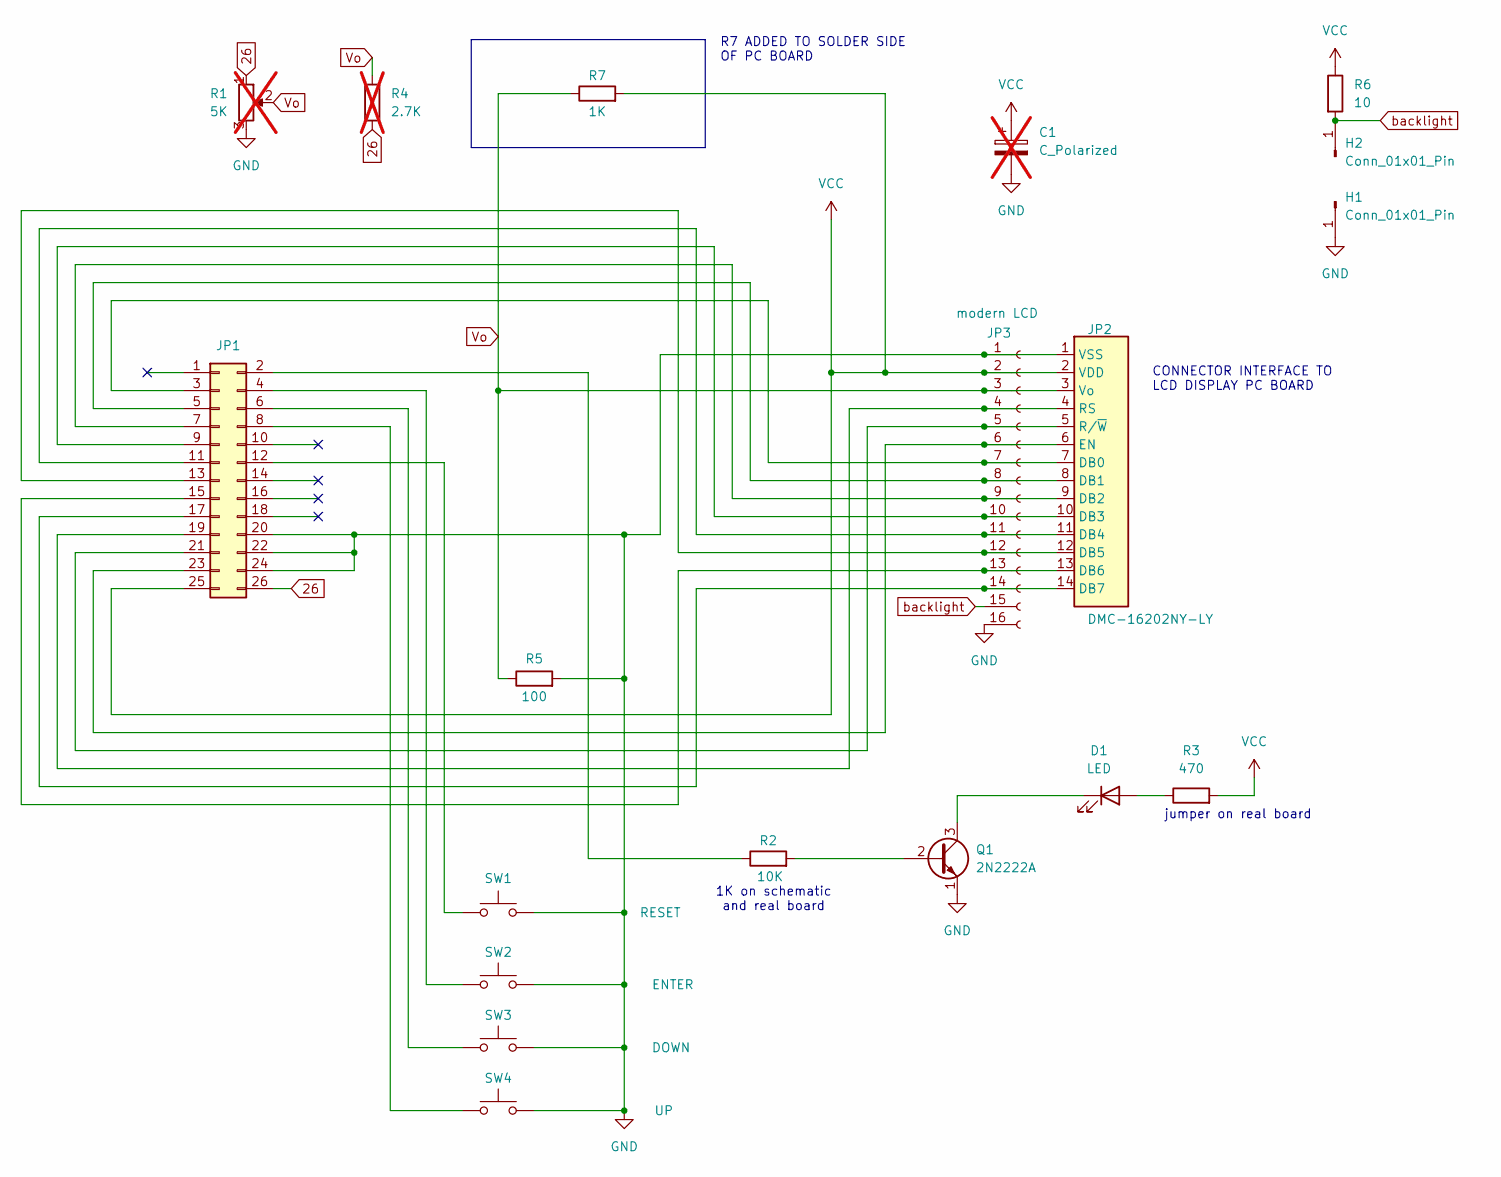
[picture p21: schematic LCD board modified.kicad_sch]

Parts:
C1: C_Polarized; CP_Radial_D8.0mm_P5.00mm; not fitted
D1: LED; PinHeader_1x02_P2.54mm_Vertical
H1, H2: Conn_01x01_Pin
JP1: Conn_02x13_Odd_Even; PinHeader_2x13_P2.54mm_Vertical
JP2: DMC-16202NY-LY; CEC LCD
JP3: modern LCD; PinHeader_1x16_P2.54mm_Vertical
Q1: 2N2222A; TO-18-3
R1: 5K; Potentiometer_Bourns_3006P_Horizontal; not fitted
R2: 10K; R_Axial_DIN0207_L6.3mm_D2.5mm_P10.16mm_Horizontal
R3: 470; R_Axial_DIN0207_L6.3mm_D2.5mm_P10.16mm_Horizontal
R4: 2.7K; R_Axial_DIN0207_L6.3mm_D2.5mm_P10.16mm_Horizontal; not fitted
R5: 100; R_Axial_DIN0207_L6.3mm_D2.5mm_P10.16mm_Horizontal
R6: 10; R_Axial_DIN0207_L6.3mm_D2.5mm_P10.16mm_Horizontal
R7: 1K; R_Axial_DIN0207_L6.3mm_D2.5mm_P10.16mm_Horizontal
SW1: RESET; CEC LCD pushbutton
SW2: ENTER; CEC LCD pushbutton
SW3: DOWN; CEC LCD pushbutton
SW4: UP; CEC LCD pushbutton

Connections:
26: JP1.26, R1.1, R4.2
GND: C1.2, H1.1, JP1.20, JP1.22, JP1.24, JP2.1 (VSS), JP3.1, JP3.16, Q1.1 (E), R1.3, R5.2, SW1.1, SW2.2, SW3.2, SW4.2
unnamed: D1.2 (A), R3.1
unnamed: D1.1 (K), Q1.3 (C)
unnamed: JP1.2, R2.1
unnamed: JP1.3, JP2.7 (DB0), JP3.7
unnamed: JP1.4, SW2.1
unnamed: JP1.5, JP2.8 (DB1), JP3.8
unnamed: JP1.6, SW3.1
unnamed: JP1.7, JP2.9 (DB2), JP3.9
unnamed: JP1.8, SW4.1
unnamed: JP1.9, JP2.10 (DB3), JP3.10
unnamed: JP1.11, JP2.11 (DB4), JP3.11
unnamed: JP1.12, SW1.2
unnamed: JP1.13, JP2.12 (DB5), JP3.12
unnamed: JP1.15, JP2.13 (DB6), JP3.13
unnamed: JP1.17, JP2.14 (DB7), JP3.14
unnamed: JP1.19, JP2.4 (RS), JP3.4
unnamed: JP1.21, JP2.5 (R/~W), JP3.5
unnamed: JP1.23, JP2.6 (EN), JP3.6
unnamed: Q1.2 (B), R2.2
VCC: C1.1, JP1.25, JP2.2 (VDD), JP3.2, R3.2, R6.1, R7.2
Vo: JP2.3 (Vo), JP3.3, R1.2, R4.1, R5.1, R7.1
backlight: H2.1, JP3.15, R6.2

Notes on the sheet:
1K on schematic and real board
R7 ADDED TO SOLDER SIDE OF PC BOARD
jumper on real board
CONNECTOR INTERFACE TO LCD DISPLAY PC BOARD

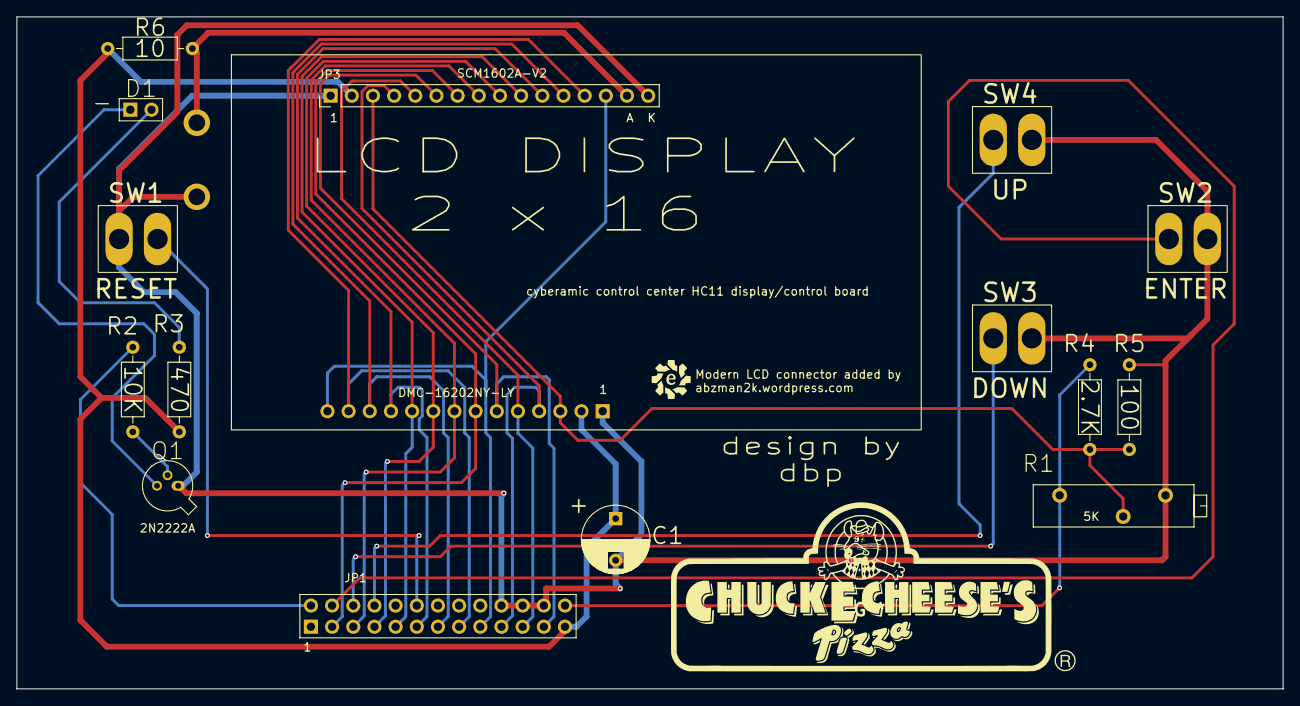
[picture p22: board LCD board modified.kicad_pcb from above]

Board: 2 copper layers, 151.9 x 80.6 mm, 18 parts (0 on the bottom side), 24 nets.

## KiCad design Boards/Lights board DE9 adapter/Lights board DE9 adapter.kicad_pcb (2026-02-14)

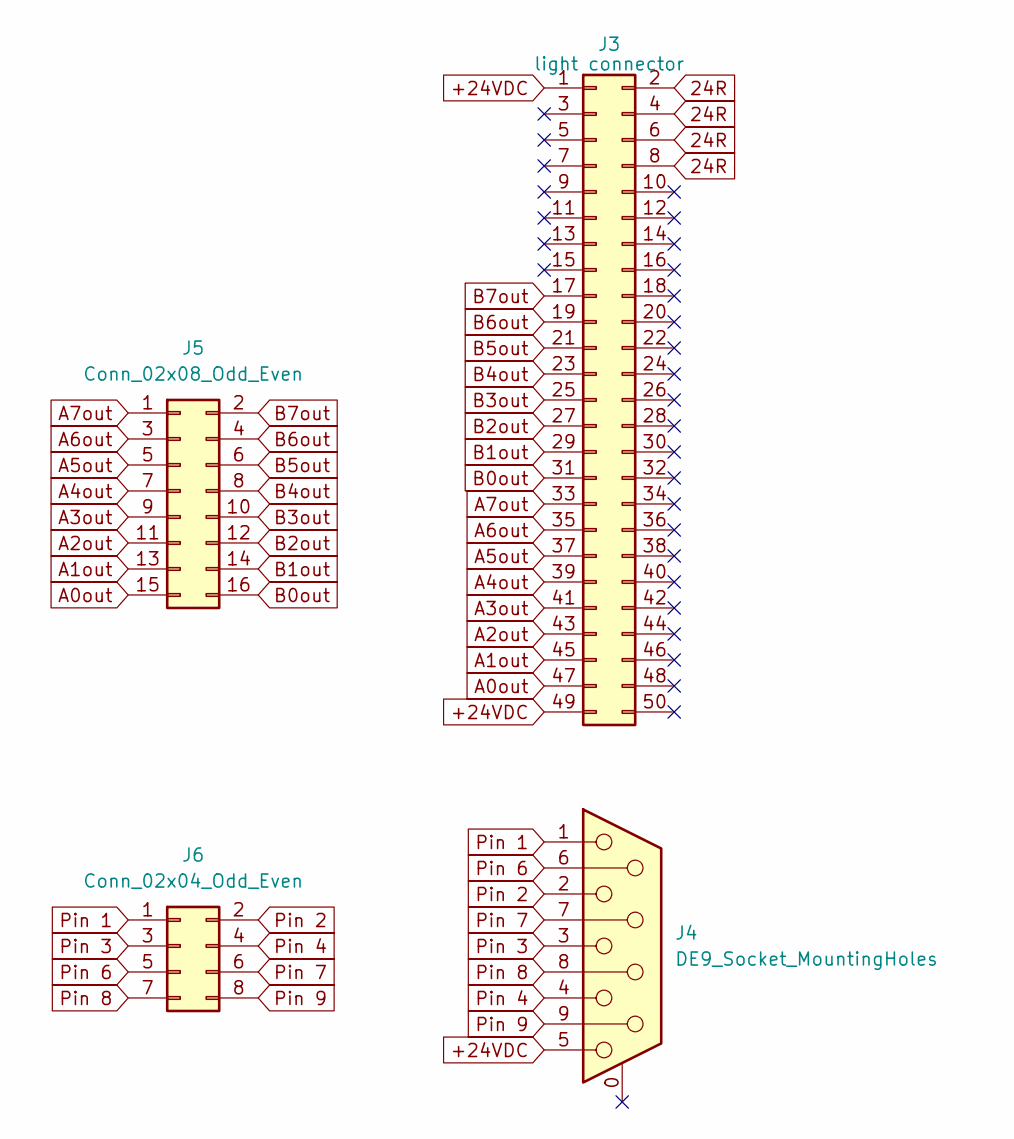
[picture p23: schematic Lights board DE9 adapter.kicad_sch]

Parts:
J3: light connector; PinSocket_2x25_P2.54mm_Horizontal
J4: DE9_Socket_MountingHoles; DSUB-9_Socket_Horizontal_P2.77x2.84mm_EdgePinOffset7.70mm_H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
J5: Conn_02x08_Odd_Even; PinHeader_2x08_P2.54mm_Horizontal
J6: Conn_02x04_Odd_Even; PinHeader_2x04_P2.54mm_Horizontal

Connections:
24R: J3.2, J3.4, J3.6, J3.8
+24VDC: J3.1, J3.49, J4.5
A0out: J3.47, J5.15
A1out: J3.45, J5.13
A2out: J3.43, J5.11
A3out: J3.41, J5.9
A4out: J3.39, J5.7
A5out: J3.37, J5.5
A6out: J3.35, J5.3
A7out: J3.33, J5.1
B0out: J3.31, J5.16
B1out: J3.29, J5.14
B2out: J3.27, J5.12
B3out: J3.25, J5.10
B4out: J3.23, J5.8
B5out: J3.21, J5.6
B6out: J3.19, J5.4
B7out: J3.17, J5.2
Pin 1: J4.1, J6.1
Pin 2: J4.2, J6.2
Pin 3: J4.3, J6.3
Pin 4: J4.4, J6.4
Pin 6: J4.6, J6.5
Pin 7: J4.7, J6.6
Pin 8: J4.8, J6.7
Pin 9: J4.9, J6.8

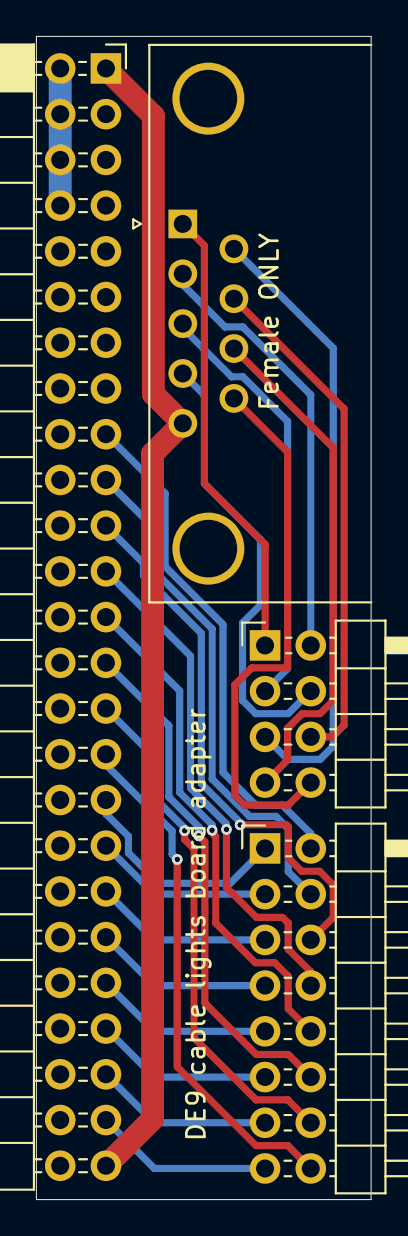
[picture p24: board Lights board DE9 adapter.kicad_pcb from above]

Board: 2 copper layers, 18.6 x 64.6 mm, 4 parts (0 on the bottom side), 26 nets.

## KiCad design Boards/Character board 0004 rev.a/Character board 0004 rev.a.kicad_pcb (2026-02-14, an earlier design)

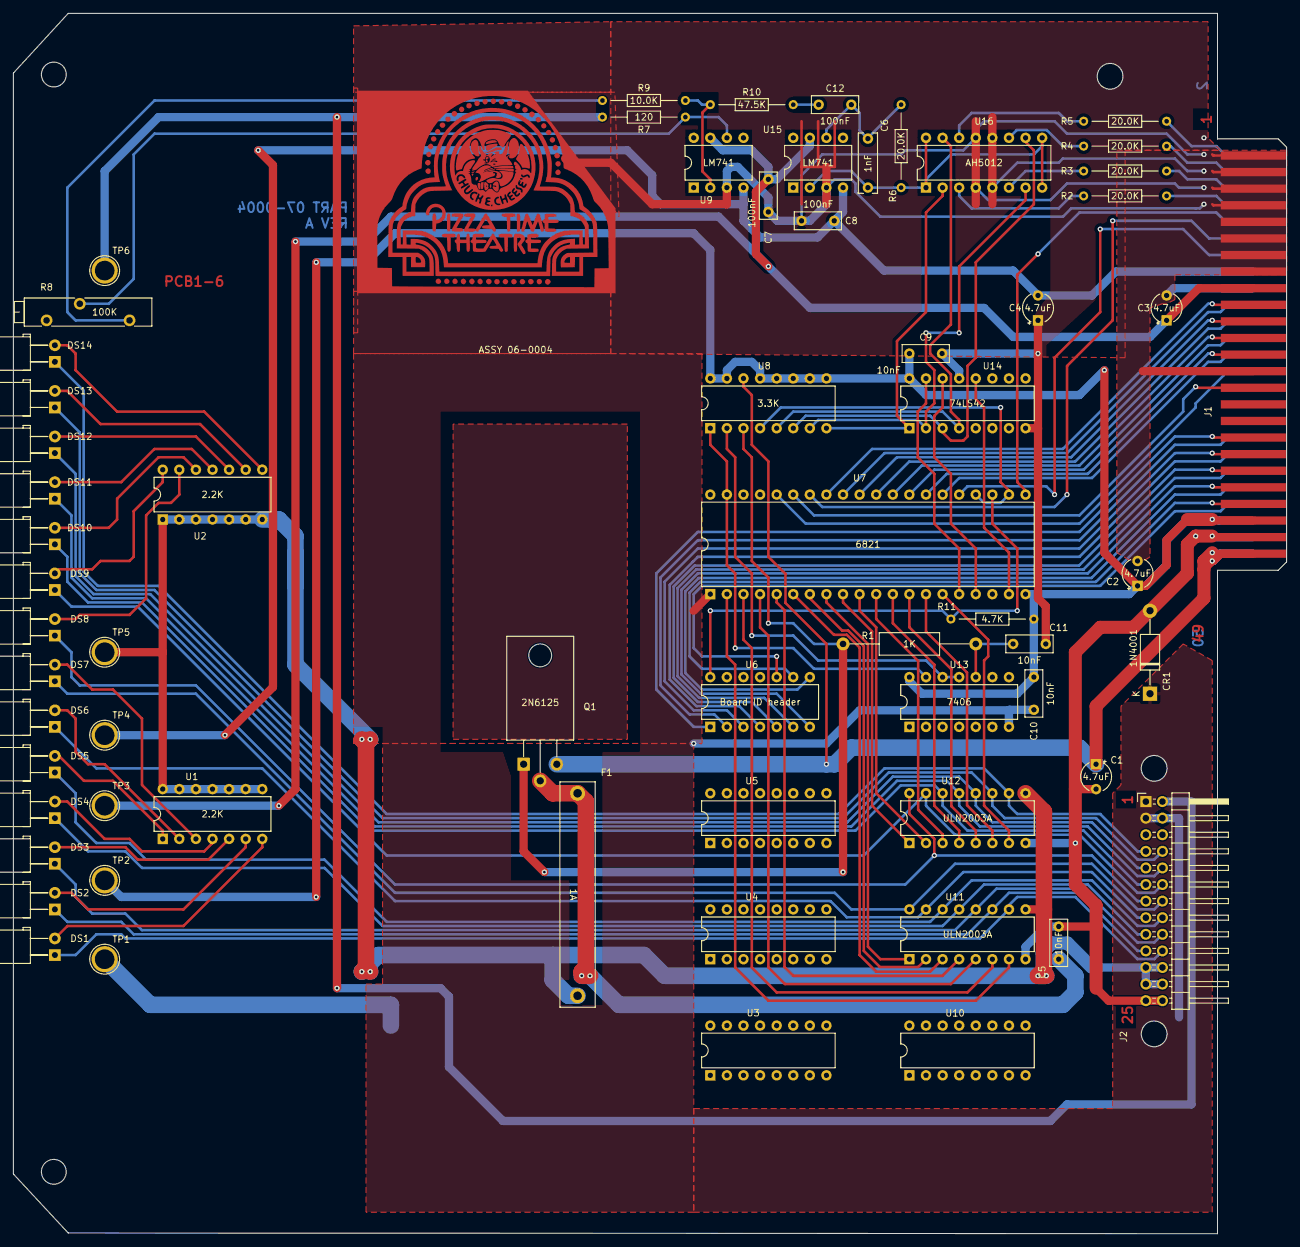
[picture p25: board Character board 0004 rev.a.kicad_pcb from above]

Board: 2 copper layers, 194.9 x 186.8 mm, 65 parts (0 on the bottom side), 101 nets.

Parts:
C1, C2, C3, C4: 4.7uF; CP_Radial_Tantal_D4mm_P3.81mm
C5, C9, C10, C11: 10nF; C_Rect_L7.0mm_W2.5mm_P5.00mm
C6: 1nF; C_Rect_L9.0mm_W2.7mm_P7.50mm_MKT
C7, C8, C12: 100nF; C_Rect_L7.0mm_W2.5mm_P5.00mm
CR1: 1N4001; D_DO-41_SOD81_P12.70mm_Horizontal
DS1, DS2, DS3, DS4, DS5, DS6, DS7, DS8, DS9, DS10, DS11, DS12, DS13, DS14: LED; LED_D5.0mm_Horizontal_O3.81mm_Z15.0mm reversed
F1: 1A; Fuseholder_Littelfuse_445_030_series_5x30mm
G1: GND; PTT white
J1: card edge; Chuck_E_Cheese_small_card_edge
J2: character connector; PinHeader_2x13_P2.54mm_Horizontal
Q1: 2N6125; TO-220-3_Horizontal_TabDown
R1: 1K; R_Axial_DIN0309_L9.0mm_D3.2mm_P20.32mm_Horizontal
R2, R3, R4, R5, R6: 20.0K; R_Axial_DIN0204_L3.6mm_D1.6mm_P12.7mm_Horizontal
R7: 120; R_Axial_DIN0204_L3.6mm_D1.6mm_P12.7mm_Horizontal
R8: 100K; Potentiometer_Bourns_3005_Horizontal
R9: 10.0K; R_Axial_DIN0204_L3.6mm_D1.6mm_P12.7mm_Horizontal
R10: 47.5K; R_Axial_DIN0204_L3.6mm_D1.6mm_P12.7mm_Horizontal
R11: 4.7K; R_Axial_DIN0204_L3.6mm_D1.6mm_P12.7mm_Horizontal
TP1: GND; TestPoint_Plated_Hole_D3.0mm
TP2: +5; TestPoint_Plated_Hole_D3.0mm
TP3: +12; TestPoint_Plated_Hole_D3.0mm
TP4: -12; TestPoint_Plated_Hole_D3.0mm
TP5: 24; TestPoint_Plated_Hole_D3.0mm
TP6: AUD; TestPoint_Plated_Hole_D3.0mm
U1, U2: 2.2K; DIP-14_W7.62mm
U3, U4, U5, U10: Unused DIP; DIP-16_W7.62mm
U6: Board ID header; DIP-14_W7.62mm
U7: 6821; DIP-40_W15.24mm
U8: 3.3K; DIP-16_W7.62mm
U9, U15: LM741; DIP-8_W7.62mm
U11, U12: ULN2003A; DIP-16_W7.62mm
U13: 7406; DIP-14_W7.62mm
U14: 74LS42; DIP-16_W7.62mm
U16: AH5012; DIP-16_W7.62mm

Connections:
5V: C2.1, C9.1, C10.1, J1.45, J1.46, R11.1, TP2.1, U7.20 (VCC), U8.9 (R8.2), U8.10 (R7.2), U8.11 (R6.2), U8.12 (R5.2), U8.13 (R4.2), U8.15 (R2.2), U8.16 (R1.2), U13.14 (VCC), U14.16 (VCC)
5Vpu: U8.2 (R2.1), U13.11, U13.12
12V: C3.1, C7.1, J1.17, TP3.1, U9.7 (V+), U15.7 (V+)
24R: C1.2, C5.1, CR1.2 (A), J1.47, J1.48, J2.25, J2.26, U11.8 (GND), U12.8 (GND)
24V: C1.1, J1.49, J1.50, Q1.3 (E), U8.14 (R3.2)
24Vout: F1.2, J2.21, J2.22, J2.23, J2.24, TP5.1, U1.8 (R7.2), U1.9 (R6.2), U1.10 (R5.2), U1.11 (R4.2), U1.12 (R3.2), U1.13 (R2.2), U1.14 (R1.2), U2.1 (R1.1), U2.2 (R2.1), U2.3 (R3.1), U2.4 (R4.1), U2.5 (R5.1), U2.6 (R6.1), U2.7 (R7.1), U11.9 (COM), U12.9 (COM)
24Vpu: Q1.1 (B), R1.1, U8.3 (R3.1)
-12V: C4.2, C8.2, J1.16, TP4.1, U9.4 (V-), U15.4 (V-)
A0out: DS1.1 (K), J2.20, U11.10 (O7)
A1out: DS2.1 (K), J2.19, U11.11 (O6)
A2out: DS3.1 (K), J2.18, U11.12 (O5)
A3out: DS4.1 (K), J2.17, U11.13 (O4)
A4out: DS5.1 (K), J2.16, U11.14 (O3)
A5out: DS6.1 (K), J2.15, U11.15 (O2)
A6out: DS7.1 (K), J2.14, U11.16 (O1)
A7out: DS8.1 (K), J2.13, U12.16 (O1)
AUD: J2.2, R7.1, TP6.1
B0out: DS9.1 (K), J2.12, U12.15 (O2)
B1out: DS10.1 (K), J2.11, U12.14 (O3)
B2out: DS11.1 (K), J2.10, U12.13 (O4)
B3out: DS12.1 (K), J2.9, U12.12 (O5)
B4out: DS13.1 (K), J2.8, U12.11 (O6)
B5out: DS14.1 (K), J2.7, U12.10 (O7)
BA0: J1.28, U7.36 (RS0)
BA1: J1.29, U7.35 (RS1)
BGOUT_AGC: J1.8, R2.1
BS1: J1.35, U6.1
BS2: J1.36, U6.2
BS3: J1.37, U6.3
BS4: J1.38, U6.4
BS5: J1.39, U6.5
BS6: J1.40, U6.6
BS7: J1.41, U6.7
BS8: J1.42, U6.8
BS9: J1.43, U6.9
BS10: J1.44, U6.10
CA2: U7.39 (CA2), U8.1 (R1.1), U13.13
CB2: U7.19 (CB2), U14.12 (A3)
CS: U7.22 (CS0), U7.24 (CS1), U8.4 (R4.1)
DBB0: J1.19, U7.33 (D0)
DBB1: J1.20, U7.32 (D1)
DBB2: J1.21, U7.31 (D2)
DBB3: J1.22, U7.30 (D3)
DBB4: J1.23, U7.29 (D4)
DBB5: J1.24, U7.28 (D5)
DBB6: J1.25, U7.27 (D6)
DBB7: J1.26, U7.26 (D7)
GND: C2.2, C3.2, C4.1, C7.2, C8.1, C9.2, C10.2, C11.2, CR1.1 (K), G1.1, J1.1, J1.3, J1.5, J1.7, J1.9, J1.11, J1.13, J1.15, J1.18, J1.27, J2.1, J2.3, J2.4, TP1.1, U7.1 (VSS), U9.3 (+), U13.7 (GND), U14.8 (GND), U14.13 (A2), U15.3 (+), U16.4, U16.5, U16.12, U16.13
unnamed: C11.1, R1.2, U13.10
unnamed: C12.1, R10.2
unnamed: C6.2, C12.2, R6.2, U15.6
unnamed: DS1.2 (A), U1.7 (R7.1)
unnamed: DS2.2 (A), U1.6 (R6.1)
unnamed: DS3.2 (A), U1.5 (R5.1)
unnamed: DS4.2 (A), U1.4 (R4.1)
unnamed: DS5.2 (A), U1.1 (R1.1)
unnamed: DS6.2 (A), U1.2 (R2.1)
unnamed: DS7.2 (A), U1.3 (R3.1)
unnamed: DS8.2 (A), U2.13 (R2.2)
unnamed: DS9.2 (A), U2.14 (R1.2)
unnamed: DS10.2 (A), U2.12 (R3.2)
unnamed: DS11.2 (A), U2.11 (R4.2)
unnamed: DS12.2 (A), U2.10 (R5.2)
unnamed: DS13.2 (A), U2.9 (R6.2)
unnamed: DS14.2 (A), U2.8 (R7.2)
unnamed: C5.2, F1.1, Q1.2 (C)
unnamed: R2.2, U16.3
unnamed: R3.2, U16.6
unnamed: R4.2, U16.11
unnamed: R5.2, U16.14
unnamed: R7.2, R8.2, U9.6
unnamed: R8.1, R9.1
unnamed: R11.2, U6.14, U7.23 (~CS2)
unnamed: R9.2, R10.1, U9.2 (-)
unnamed: U8.8 (R8.1), U14.1 (0), U16.2
unnamed: U8.7 (R7.1), U14.2 (1), U16.7
unnamed: U8.6 (R6.1), U14.3 (2), U16.10
unnamed: U8.5 (R5.1), U14.4 (3), U16.15
unnamed: C6.1, R6.1, U15.2 (-), U16.1, U16.8, U16.9, U16.16
PA0: U7.2 (PA0), U11.7 (I7)
PA1: U7.3 (PA1), U11.6 (I6)
PA2: U7.4 (PA2), U11.5 (I5)
PA3: U7.5 (PA3), U11.4 (I4)
PA4: U7.6 (PA4), U11.3 (I3)
PA5: U7.7 (PA5), U11.2 (I2)
PA6: U7.8 (PA6), U11.1 (I1)
PA7: U7.9 (PA7), U12.1 (I1)
PB0: U7.10 (PB0), U12.2 (I2)
PB1: U7.11 (PB1), U12.3 (I3)
PB2: U7.12 (PB2), U12.4 (I4)
PB3: U7.13 (PB3), U12.5 (I5)
PB4: U7.14 (PB4), U12.6 (I6)
PB5: U7.15 (PB5), U12.7 (I7)
PB6: U7.16 (PB6), U14.15 (A0)
PB7: U7.17 (PB7), U14.14 (A1)
PHI2: J1.14, U7.25 (ENABLE)
R2R_audio_AGC: J1.6, R3.1
R/~W: J1.10, U7.21 (R/~W)
aux1_AGC: J1.2, R5.1
aux2_AGC: J1.4, R4.1
~MRST: J1.12, U7.34 (~RESET)

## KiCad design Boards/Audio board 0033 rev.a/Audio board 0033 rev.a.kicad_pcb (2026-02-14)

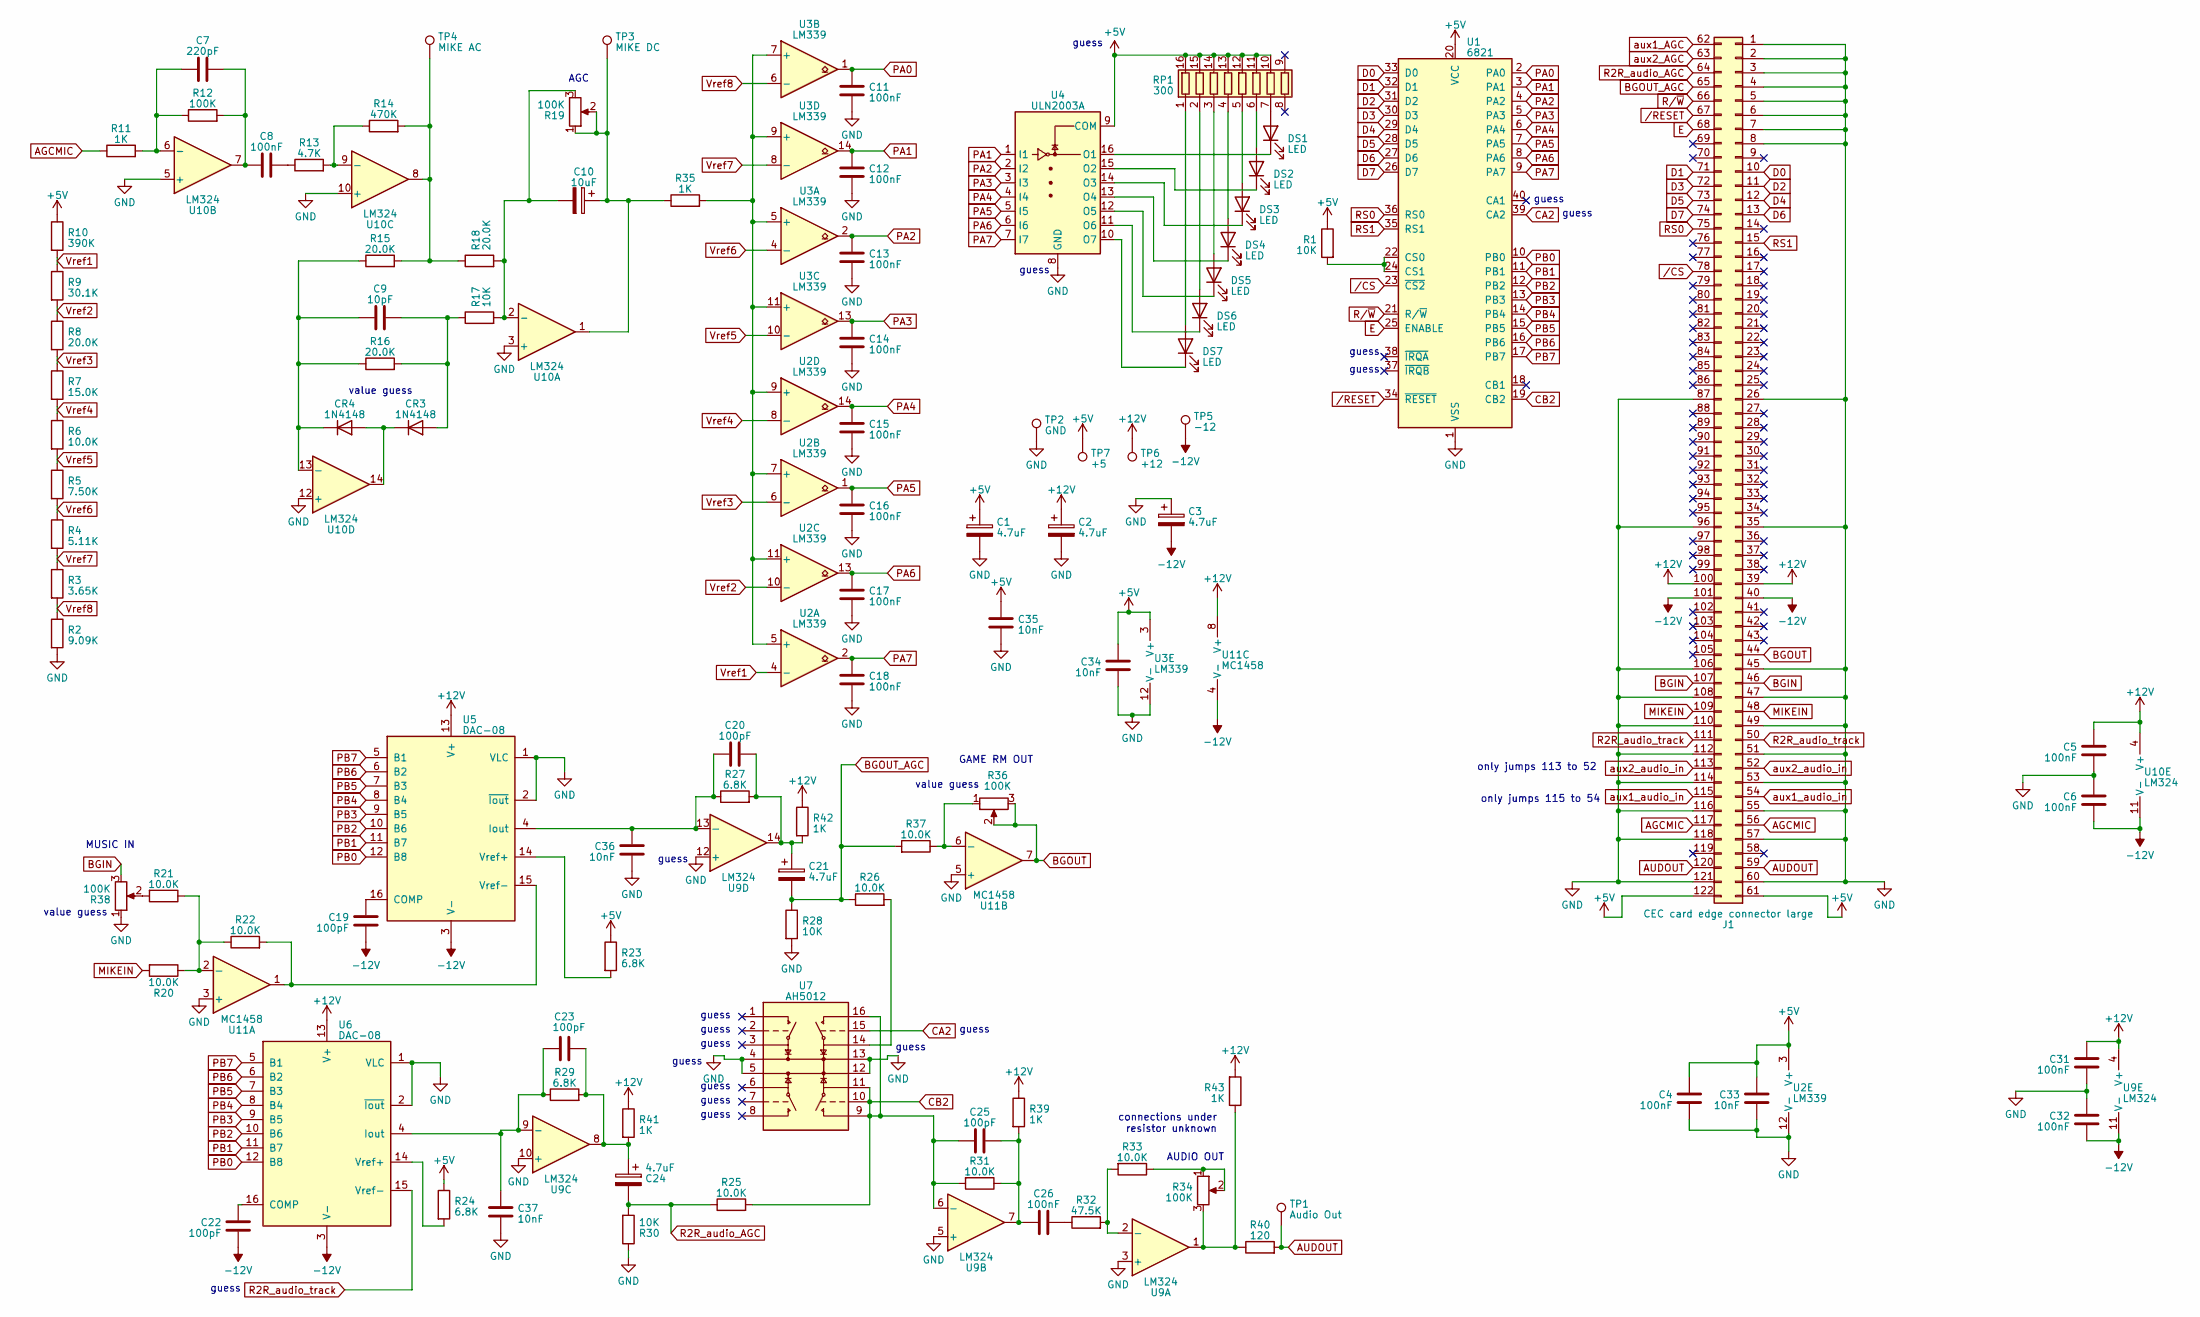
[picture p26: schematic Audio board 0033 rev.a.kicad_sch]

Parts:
C1, C2, C3, C21, C24: 4.7uF; CP_Radial_Tantal_D4mm_P3.81mm
C4, C5, C6, C8, C11, C12, C13, C14, C15, C16, C17, C18, C26, C31, C32: 100nF; C_Disc_D3.0mm_W1.6mm_P2.50mm
C7: 220pF; C_Rect_L7.0mm_W2.5mm_P5.00mm
C9: 10pF; C_Rect_L7.0mm_W2.5mm_P5.00mm
C10: 10uF; CP_Axial_L10.0mm_D4.5mm_P27.94mm_Horizontal
C19, C20, C22, C23, C25: 100pF; C_Rect_L7.0mm_W2.5mm_P5.00mm
C33, C34, C35: 10nF; C_Rect_L9.0mm_W2.5mm_P7.50mm_MKT
C36, C37: 10nF; C_Disc_D3.0mm_W1.6mm_P2.50mm
CR3, CR4: 1N4148; D_DO-35_SOD27_P7.62mm_Horizontal
DS1, DS2, DS3, DS4, DS5, DS6, DS7: LED; LED_D5.0mm_Horizontal_O3.81mm_Z15.0mm
J1: CEC card edge connector large; Chuck_E_Cheese_large_card_edge
R1, R17, R28, R30: 10K; R_Axial_DIN0309_L9.0mm_D3.2mm_P12.70mm_Horizontal
R2: 9.09K; R_Axial_DIN0309_L9.0mm_D3.2mm_P12.70mm_Horizontal
R3: 3.65K; R_Axial_DIN0309_L9.0mm_D3.2mm_P12.70mm_Horizontal
R4: 5.11K; R_Axial_DIN0309_L9.0mm_D3.2mm_P12.70mm_Horizontal
R5: 7.50K; R_Axial_DIN0309_L9.0mm_D3.2mm_P12.70mm_Horizontal
R6, R20, R21, R22, R25, R26, R31, R33, R37: 10.0K; R_Axial_DIN0309_L9.0mm_D3.2mm_P12.70mm_Horizontal
R7: 15.0K; R_Axial_DIN0309_L9.0mm_D3.2mm_P12.70mm_Horizontal
R8, R15, R16, R18: 20.0K; R_Axial_DIN0309_L9.0mm_D3.2mm_P12.70mm_Horizontal
R9: 30.1K; R_Axial_DIN0309_L9.0mm_D3.2mm_P12.70mm_Horizontal
R10: 390K; R_Axial_DIN0309_L9.0mm_D3.2mm_P12.70mm_Horizontal
R11, R35, R39, R41, R42, R43: 1K; R_Axial_DIN0309_L9.0mm_D3.2mm_P12.70mm_Horizontal
R12: 100K; R_Axial_DIN0309_L9.0mm_D3.2mm_P12.70mm_Horizontal
R13: 4.7K; R_Axial_DIN0309_L9.0mm_D3.2mm_P12.70mm_Horizontal
R14: 470K; R_Axial_DIN0309_L9.0mm_D3.2mm_P12.70mm_Horizontal
R19, R34, R36, R38: 100K; Potentiometer_Bourns_3005_Horizontal
R23, R24, R27, R29: 6.8K; R_Axial_DIN0309_L9.0mm_D3.2mm_P12.70mm_Horizontal
R32: 47.5K; R_Axial_DIN0309_L9.0mm_D3.2mm_P12.70mm_Horizontal
R40: 120; R_Axial_DIN0309_L9.0mm_D3.2mm_P12.70mm_Horizontal
RP1: 300; DIP-16_W7.62mm
TP1: Audio Out; TestPoint_Plated_Hole_D3.0mm
TP2: GND; TestPoint_Plated_Hole_D3.0mm
TP3: MIKE DC; TestPoint_Plated_Hole_D3.0mm
TP4: MIKE AC; TestPoint_Plated_Hole_D3.0mm
TP5: -12; TestPoint_Plated_Hole_D3.0mm
TP6: +12; TestPoint_Plated_Hole_D3.0mm
TP7: +5; TestPoint_Plated_Hole_D3.0mm
U1: 6821; DIP-40_W15.24mm
U2, U3: LM339; DIP-14_W7.62mm
U4: ULN2003A; DIP-16_W7.62mm
U5, U6: DAC-08; DIP-16_W7.62mm
U7: AH5012; DIP-16_W7.62mm
U9, U10: LM324; DIP-14_W7.62mm
U11: MC1458; DIP-8_W7.62mm

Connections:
+5V: C1.1, C4.1, C33.1, C34.1, C35.1, J1.61, J1.122, R1.1, R10.1, R23.1, R24.1, RP1.10 (R7.2), RP1.11 (R6.2), RP1.12 (R5.2), RP1.13 (R4.2), RP1.14 (R3.2), RP1.15 (R2.2), RP1.16 (R1.2), TP7.1, U1.20 (VCC), U2.3 (V+), U3.3 (V+), U4.9 (COM)
+12V: C2.1, C5.1, C31.2, J1.39, J1.100, R39.1, R41.1, R42.1, R43.2, TP6.1, U5.13 (V+), U6.13 (V+), U9.4 (V+), U10.4 (V+), U11.8 (V+)
-12V: C3.2, C6.2, C19.2, C22.2, C32.1, J1.40, J1.101, TP5.1, U5.3 (V-), U6.3 (V-), U9.11 (V-), U10.11 (V-), U11.4 (V-)
AGCMIC: J1.56, J1.117, R11.1
AUDOUT: J1.59, J1.120, R40.2, TP1.1
BGIN: J1.46, J1.107, R38.3
BGOUT: J1.44, R36.2, R36.3, U11.7
CA2: U1.39 (CA2), U7.15
D0: J1.10, U1.33 (D0)
D1: J1.71, U1.32 (D1)
D2: J1.11, U1.31 (D2)
D3: J1.72, U1.30 (D3)
D4: J1.12, U1.29 (D4)
D5: J1.73, U1.28 (D5)
D6: J1.13, U1.27 (D6)
D7: J1.74, U1.26 (D7)
E: J1.68, U1.25 (ENABLE)
GND: C1.2, C2.2, C3.1, C4.2, C5.2, C6.1, C11.2, C12.2, C13.2, C14.2, C15.2, C16.2, C17.2, C18.2, C31.1, C32.2, C33.2, C34.2, C35.2, C36.1, C37.1, J1.1, J1.2, J1.3, J1.4, J1.5, J1.6, J1.7, J1.8, J1.26, J1.35, J1.45, J1.47, J1.49, J1.51, J1.53, J1.55, J1.57, J1.60, J1.87, J1.96, J1.106, J1.108, J1.110, J1.112, J1.114, J1.116, J1.118, J1.121, R2.2, R28.2, R30.1, R38.1, TP2.1, U1.1 (VSS), U2.12 (V-), U3.12 (V-), U4.8 (GND), U5.1 (VLC), U5.2 (~Iout), U6.1 (VLC), U6.2 (~Iout), U7.4, U7.5, U7.12, U7.13, U9.3 (+), U9.5 (+), U9.10 (+), U9.12 (+), U10.3 (+), U10.5 (+), U10.10 (+), U10.12 (+), U11.3 (+), U11.5 (+)
MIKEIN: J1.48, J1.109, R20.2
unnamed: C7.2, C8.1, R12.2, U10.7
unnamed: C8.2, R13.1
unnamed: C10.1, R19.1, R19.2, R35.1, TP3.1, U10.1
unnamed: C20.2, C21.1, R27.2, R42.2, U9.14
unnamed: C23.2, C24.1, R29.2, R41.2, U9.8
unnamed: C25.1, C26.1, R31.1, R39.2, U9.7
unnamed: C26.2, R32.1
unnamed: C9.2, CR3.2 (A), R16.2, R17.1
unnamed: CR3.1 (K), CR4.2 (A), U10.14
unnamed: C9.1, CR4.1 (K), R15.1, R16.1, U10.13 (-)
unnamed: DS1.2 (A), RP1.7 (R7.1)
unnamed: DS1.1 (K), U4.16 (O1)
unnamed: DS2.2 (A), RP1.6 (R6.1)
unnamed: DS2.1 (K), U4.15 (O2)
unnamed: DS3.2 (A), RP1.5 (R5.1)
unnamed: DS3.1 (K), U4.14 (O3)
unnamed: DS4.2 (A), RP1.4 (R4.1)
unnamed: DS4.1 (K), U4.13 (O4)
unnamed: DS5.2 (A), RP1.3 (R3.1)
unnamed: DS5.1 (K), U4.12 (O5)
unnamed: DS6.2 (A), RP1.2 (R2.1)
unnamed: DS6.1 (K), U4.11 (O6)
unnamed: DS7.2 (A), RP1.1 (R1.1)
unnamed: DS7.1 (K), U4.10 (O7)
unnamed: R14.2, R15.2, R18.1, TP4.1, U10.8
unnamed: R21.2, R38.2
unnamed: R26.2, U7.14
unnamed: R33.1, R34.1, R34.2
unnamed: R34.3, R40.1, R43.1, U9.1
unnamed: R1.2, U1.22 (CS0), U1.24 (CS1)
unnamed: R35.2, U2.5 (+), U2.7 (+), U2.9 (+), U2.11 (+), U3.5 (+), U3.7 (+), U3.9 (+), U3.11 (+)
unnamed: C19.1, U5.16 (COMP)
unnamed: C20.1, C36.2, R27.1, U5.4 (Iout), U9.13 (-)
unnamed: R23.2, U5.14 (Vref+)
unnamed: R22.2, U5.15 (Vref-), U11.1
unnamed: C22.1, U6.16 (COMP)
unnamed: C23.1, C37.2, R29.1, U6.4 (Iout), U9.9 (-)
unnamed: R24.2, U6.14 (Vref+)
unnamed: R32.2, R33.2, U9.2 (-)
unnamed: C10.2, R17.2, R18.2, R19.3, U10.2 (-)
unnamed: C7.1, R11.2, R12.1, U10.6 (-)
unnamed: R13.2, R14.1, U10.9 (-)
unnamed: R20.1, R21.1, R22.1, U11.2 (-)
unnamed: R36.1, R37.1, U11.6 (-)
PA0: C11.1, U1.2 (PA0), U3.1
PA1: C12.1, U1.3 (PA1), U3.14, U4.1 (I1)
PA2: C13.1, U1.4 (PA2), U3.2, U4.2 (I2)
PA3: C14.1, U1.5 (PA3), U3.13, U4.3 (I3)
PA4: C15.1, U1.6 (PA4), U2.14, U4.4 (I4)
PA5: C16.1, U1.7 (PA5), U2.1, U4.5 (I5)
PA6: C17.1, U1.8 (PA6), U2.13, U4.6 (I6)
PA7: C18.1, U1.9 (PA7), U2.2, U4.7 (I7)
PB0: U1.10 (PB0), U5.12 (B8), U6.12 (B8)
PB1: U1.11 (PB1), U5.11 (B7), U6.11 (B7)
PB2: U1.12 (PB2), U5.10 (B6), U6.10 (B6)
PB3: U1.13 (PB3), U5.9 (B5), U6.9 (B5)
PB4: U1.14 (PB4), U5.8 (B4), U6.8 (B4)
PB5: U1.15 (PB5), U5.7 (B3), U6.7 (B3)
PB6: U1.16 (PB6), U5.6 (B2), U6.6 (B2)
PB7: U1.17 (PB7), U5.5 (B1), U6.5 (B1)
Pin 64: C24.2, J1.64, R25.1, R30.2
Pin 65: C21.2, J1.65, R26.1, R28.1, R37.2
Pin 113: J1.52, J1.113
Pin 115: J1.54, J1.115
R2R_audio_track: J1.50, J1.111, U6.15 (Vref-)
RS0: J1.75, U1.36 (RS0)
RS1: J1.15, U1.35 (RS1)
R/~W: J1.66, U1.21 (R/~W)
Vref1: R9.1, R10.2, U2.4 (-)
Vref2: R8.1, R9.2, U2.10 (-)
Vref3: R7.1, R8.2, U2.6 (-)
Vref4: R6.1, R7.2, U2.8 (-)
Vref5: R5.1, R6.2, U3.10 (-)
Vref6: R4.1, R5.2, U3.4 (-)
Vref7: R3.1, R4.2, U3.8 (-)
Vref8: R2.1, R3.2, U3.6 (-)
/CS: J1.78, U1.23 (~CS2)
/RESET: J1.67, U1.34 (~RESET)

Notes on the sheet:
guess
value guess
AGC
AUDIO OUT
GAME RM OUT
only jumps 115 to 54
connections under resistor unknown
only jumps 113 to 52
MUSIC IN

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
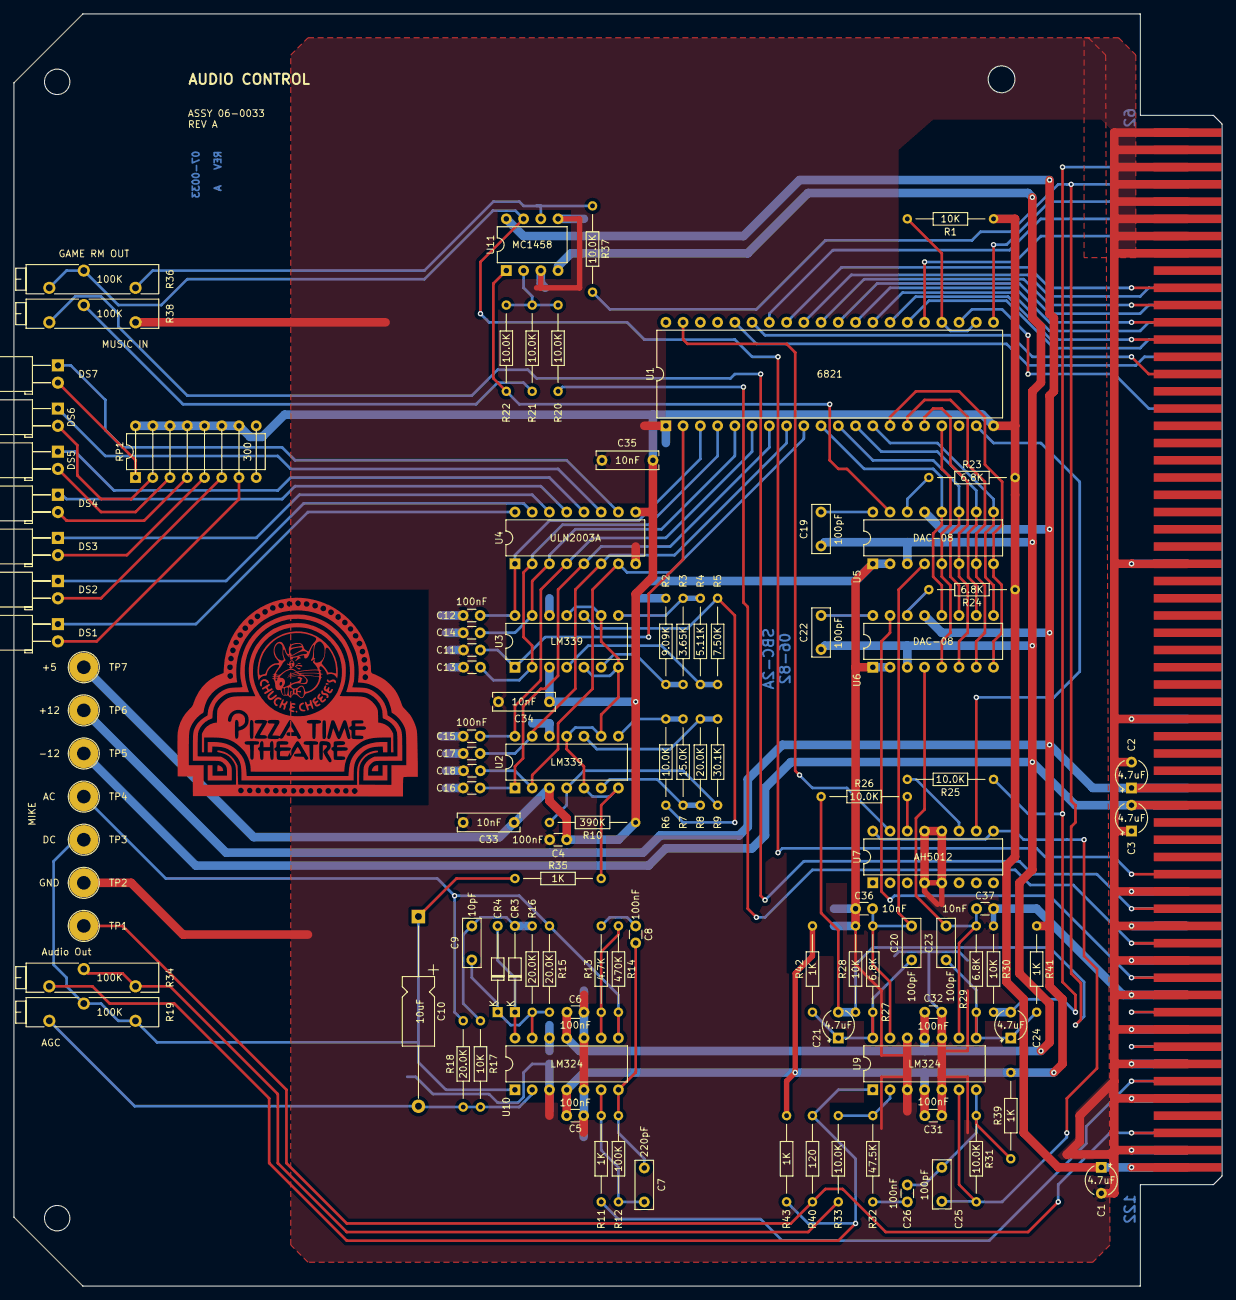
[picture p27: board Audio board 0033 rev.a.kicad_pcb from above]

Board: 2 copper layers, 177.9 x 187.4 mm, 104 parts (0 on the bottom side), 100 nets.

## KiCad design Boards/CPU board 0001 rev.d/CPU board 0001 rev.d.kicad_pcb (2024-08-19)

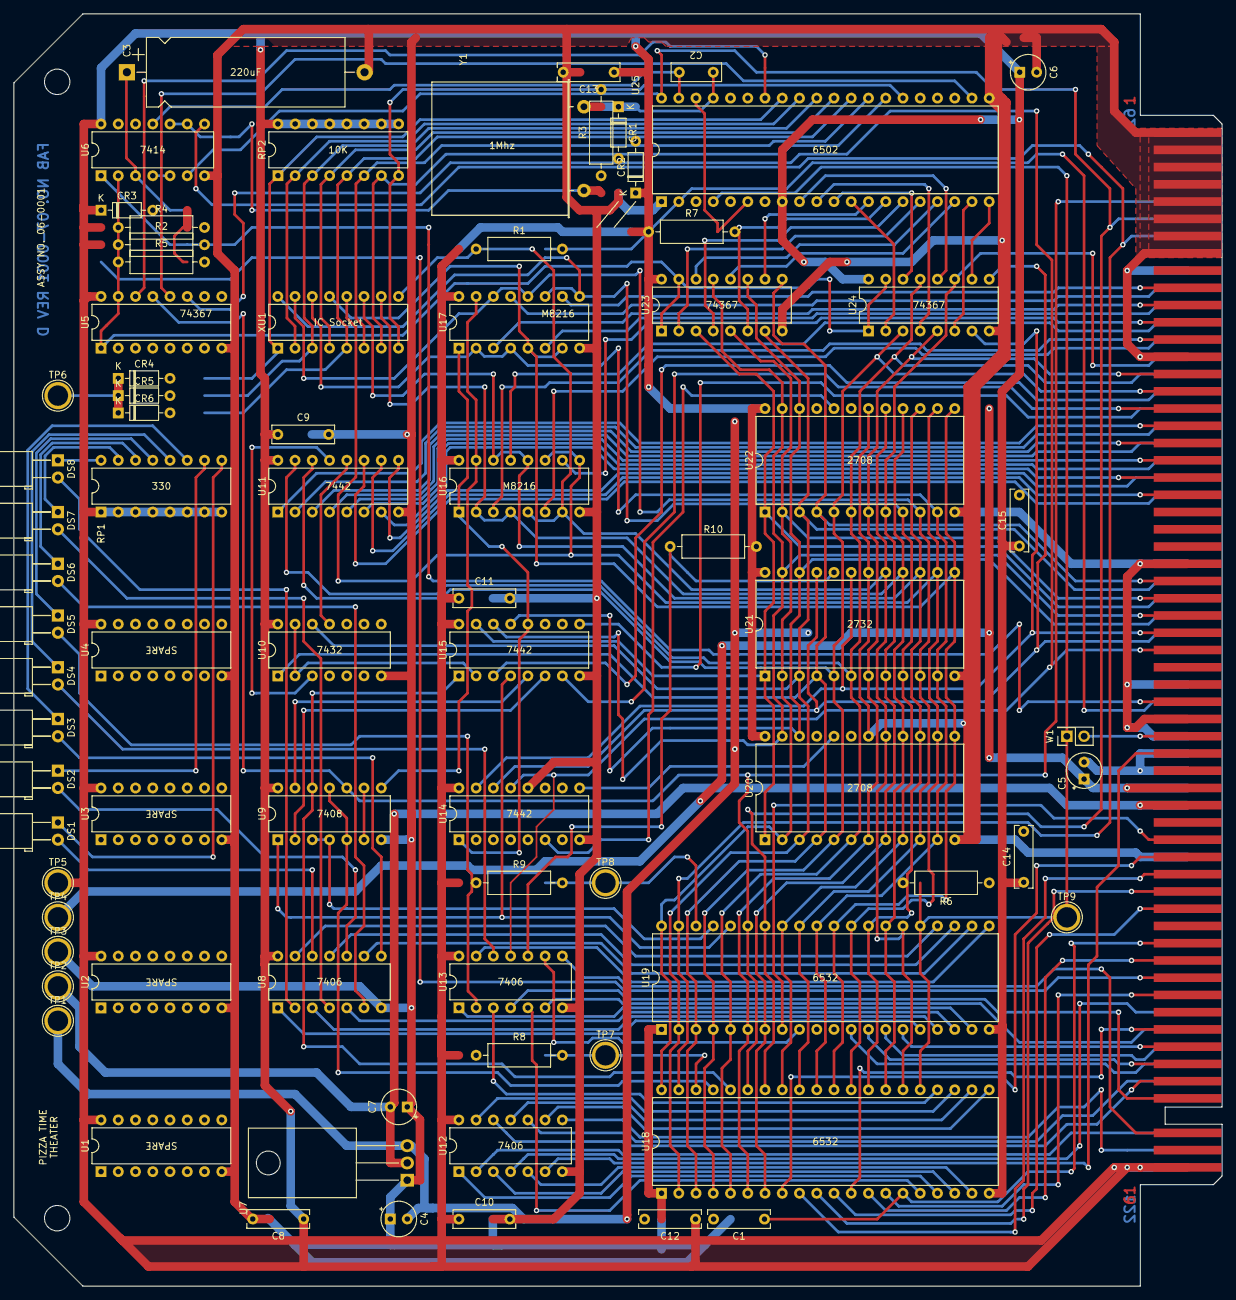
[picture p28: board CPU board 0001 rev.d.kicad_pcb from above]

Board: 2 copper layers, 177.9 x 187.4 mm, 79 parts (0 on the bottom side), 157 nets.

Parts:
C1, C8, C9, C10, C11, C12, C13, C14, C15: 100nF; C_Rect_L9.0mm_W2.5mm_P7.50mm_MKT
C2: 10pF; C_Rect_L7.2mm_W2.5mm_P5.00mm_FKS2_FKP2_MKS2_MKP2
C3: 220uF; CP_Axial_L29.0mm_D10.0mm_P35.00mm_Horizontal
C4, C5, C6, C7: 4.7uF; CP_Radial_Tantal_D5.0mm_P2.50mm
CR1, CR2, CR3, CR4, CR5, CR6: 1N914; D_DO-35_SOD27_P7.62mm_Horizontal
DS1, DS2, DS3, DS4, DS5, DS6, DS7, DS8: LED; LED_D5.0mm_Horizontal_O3.81mm_Z15.0mm
J1: CEC card edge connector large; Chuck_E_Cheese_large_card_edge
R1, R2, R4, R6, R7, R8, R9: 4.7K; R_Axial_DIN0309_L9.0mm_D3.2mm_P12.70mm_Horizontal
R3: 330K; R_Axial_DIN0309_L9.0mm_D3.2mm_P12.70mm_Horizontal
R5: 100; R_Axial_DIN0309_L9.0mm_D3.2mm_P12.70mm_Horizontal
R10: 1K; R_Axial_DIN0309_L9.0mm_D3.2mm_P12.70mm_Horizontal
RP1: 330; DIP-16_W7.62mm
RP2: 10K; DIP-16_W7.62mm
TP1: -5v; TestPoint_Plated_Hole_D3.0mm
TP2: -12v; TestPoint_Plated_Hole_D3.0mm
TP3: GND; TestPoint_Plated_Hole_D3.0mm
TP4: +12v; TestPoint_Plated_Hole_D3.0mm
TP5: +5v; TestPoint_Plated_Hole_D3.0mm
TP6: ~{0/2/4}; TestPoint_Plated_Hole_D3.0mm
TP7: U18 CS; TestPoint_Plated_Hole_D3.0mm
TP8: U19 CS; TestPoint_Plated_Hole_D3.0mm
TP9: IRQ; TestPoint_Plated_Hole_D3.0mm
U1, U2, U3, U4: SPARE; DIP-16_W7.62mm
U5, U23, U24: 74367; DIP-16_W7.62mm
U6: 7414; DIP-14_W7.62mm
U7: LM7905_TO220; TO-220-3_Horizontal_TabDown
U8, U12, U13: 7406; DIP-14_W7.62mm
U9: 7408; DIP-14_W7.62mm
U10: 7432; DIP-14_W7.62mm
U11, U14, U15: 7442; DIP-16_W7.62mm
U16, U17: M8216; DIP-16_W7.62mm
U18, U19: 6532; DIP-40_W15.24mm
U20, U22: 2708; DIP-24_W15.24mm
U21: 2732; DIP-24_W15.24mm
U25: 6502; DIP-40_W15.24mm
W1: IRQ; PinSocket_2x01_P2.54mm_Vertical
XU1: IC Socket; DIP-16_W7.62mm
Y1: 1Mhz; Crystal_HC33-U_Horizontal

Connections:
+5V: C6.1, C8.1, C9.1, C10.1, C11.1, C12.1, C13.1, C14.1, C15.1, CR2.1 (K), CR3.1 (K), J1.61, J1.122, R1.1, R2.1, R4.1, R6.1, R7.1, R8.1, R9.1, R10.1, RP1.1 (R1.1), RP1.2 (R2.1), RP1.3 (R3.1), RP1.4 (R4.1), RP1.5 (R5.1), RP1.6 (R6.1), RP1.7 (R7.1), RP1.8 (R8.1), RP2.9 (R8.2), RP2.10 (R7.2), RP2.11 (R6.2), RP2.12 (R5.2), RP2.13 (R4.2), RP2.14 (R3.2), RP2.15 (R2.2), RP2.16 (R1.2), TP5.1, U1.16 (R1.2), U2.16 (R1.2), U3.16 (R1.2), U4.16 (R1.2), U5.16 (VCC), U6.14 (VCC), U8.14 (VCC), U9.14 (VCC), U10.14 (VCC), U11.16 (VCC), U12.14 (VCC), U13.14 (VCC), U14.16 (VCC), U15.16 (VCC), U16.16 (VCC), U17.16 (VCC), U18.20 (Vcc), U19.20 (Vcc), U20.24 (VCC), U21.24 (VCC), U22.24 (VCC), U23.16 (VCC), U24.16 (VCC), U25.8 (Vcc)
+12V: C5.1, J1.39, J1.100, TP4.1
-5V: C4.2, TP1.1, U7.3 (VO)
-12V: C7.2, J1.40, J1.101, TP2.1, U7.2 (VI)
A0: U24.12 (I5), U25.9 (A0)
A1: U24.4 (I2), U25.10 (A1)
A2: U24.14 (I6), U25.11 (A2)
A3: U24.2 (I1), U25.12 (A3)
A4: U23.10 (I4), U25.13 (A4)
A5: U23.6 (I3), U25.14 (A5)
A6: U23.4 (I2), U25.15 (A6)
A7: U23.2 (I1), U25.16 (A7)
A8: U23.14 (I6), U25.17 (A8)
A9: U23.12 (I5), U25.18 (A9)
A10: U24.6 (I3), U25.19 (A10)
A11: U24.10 (I4), U25.20 (A11)
A12: U5.12 (I5), U25.22 (A12)
AGC 1: J1.116, U19.12 (PA4)
AGC 2: J1.55, U19.13 (PA5)
AGC 4: J1.115, U19.14 (PA6)
AGC 8: J1.54, U19.15 (PA7)
AUDIO: J1.78, U15.9 (7)
B'DAY in: J1.44, U18.9 (PA1)
B'DAY out: J1.56, U12.12
BA0: J1.75, U18.7 (A0), U19.7 (A0), U20.8 (A0), U21.8 (A0), U22.8 (A0), U24.11 (O5b)
BA1: J1.15, U18.6 (A1), U19.6 (A1), U20.7 (A1), U21.7 (A1), U22.7 (A1), U24.5 (O2a)
BA2: J1.76, U11.15 (A0), U18.5 (A2), U19.5 (A2), U20.6 (A2), U21.6 (A2), U22.6 (A2), U24.13 (O6b)
BA3: J1.16, U11.14 (A1), U18.4 (A3), U19.4 (A3), U20.5 (A3), U21.5 (A3), U22.5 (A3), U24.3 (O1a)
BA4: J1.27, U10.1, U18.3 (A4), U19.3 (A4), U20.4 (A4), U21.4 (A4), U22.4 (A4), U23.9 (O4a)
BA5: J1.88, U10.12, U18.2 (A5), U19.2 (A5), U20.3 (A5), U21.3 (A5), U22.3 (A5), U23.7 (O3a)
BA6: J1.28, U18.40 (A6), U19.40 (A6), U20.2 (A6), U21.2 (A6), U22.2 (A6), U23.5 (O2a)
BA7: J1.89, U15.15 (A0), U20.1 (A7), U21.1 (A7), U22.1 (A7), U23.3 (O1a)
BA8: J1.29, U15.14 (A1), U20.23 (A8), U21.23 (A8), U22.23 (A8), U23.13 (O6b)
BA9: J1.90, U15.13 (A2), U20.22 (A9), U21.22 (A9), U22.22 (A9), U23.11 (O5b)
BA10: J1.30, U14.15 (A0), U21.19 (A10), U24.7 (O3a)
BA11: J1.91, U14.14 (A1), U21.21 (A11), U24.9 (O4a)
BA12: J1.31, U5.11 (O5b), U13.11, U14.13 (A2)
BS1: J1.18, U11.1 (0)
BS2: J1.79, U11.2 (1)
BS3: J1.19, U11.3 (2)
BS4: J1.80, U11.4 (3)
BS5: J1.20, U11.5 (4)
BS6: J1.81, U11.6 (5)
BS7: J1.21, U11.7 (6)
BS8: J1.82, U11.9 (7)
BS9: J1.22, U11.10 (8)
BS10: J1.83, U11.11 (9)
CHEER in: J1.43, U18.8 (PA0)
CHEER out: J1.57, U13.4
D0: U17.9 (DI2), U17.11 (DO2), U18.33 (D0), U19.33 (D0), U20.9 (D0), U21.9 (D0), U22.9 (D0), XU1.16 (R1.2)
D1: U17.12 (DI3), U17.14 (DO3), U18.32 (D1), U19.32 (D1), U20.10 (D1), U21.10 (D1), U22.10 (D1), XU1.15 (R2.2)
D2: U17.2 (DO0), U17.4 (DI0), U18.31 (D2), U19.31 (D2), U20.11 (D2), U21.11 (D2), U22.11 (D2), XU1.14 (R3.2)
D3: U17.5 (DO1), U17.7 (DI1), U18.30 (D3), U19.30 (D3), U20.13 (D3), U21.13 (D3), U22.13 (D3), XU1.13 (R4.2)
D4: U16.9 (DI2), U16.11 (DO2), U18.29 (D4), U19.29 (D4), U20.14 (D4), U21.14 (D4), U22.14 (D4), XU1.12 (R5.2)
D5: U16.12 (DI3), U16.14 (DO3), U18.28 (D5), U19.28 (D5), U20.15 (D5), U21.15 (D5), U22.15 (D5), XU1.11 (R6.2)
D6: U16.2 (DO0), U16.4 (DI0), U18.27 (D6), U19.27 (D6), U20.16 (D6), U21.16 (D6), U22.16 (D6), XU1.10 (R7.2)
D7: U16.5 (DO1), U16.7 (DI1), U18.26 (D7), U19.26 (D7), U20.17 (D7), U21.17 (D7), U22.17 (D7), XU1.9 (R8.2)
DB0: J1.10, U17.10 (DB2)
DB1: J1.71, U17.13 (DB3)
DB2: J1.11, U17.3 (DB0)
DB3: J1.72, U17.6 (DB1)
DB4: J1.12, U16.10 (DB2)
DB5: J1.73, U16.13 (DB3)
DB6: J1.13, U16.3 (DB0)
DB7: J1.74, U16.6 (DB1)
DIAG in: J1.53, U18.12 (PA4)
DIAG out: J1.37, U12.6
GND: C1.2, C3.2, C4.1, C5.2, C6.2, C7.1, C8.2, C9.2, C10.2, C11.2, C12.2, C13.2, C14.2, C15.2, CR1.2 (A), J1.1, J1.2, J1.3, J1.4, J1.5, J1.6, J1.7, J1.8, J1.14, J1.26, J1.35, J1.70, J1.87, J1.94, J1.97, J1.98, J1.99, J1.103, J1.104, J1.105, J1.106, J1.107, J1.108, J1.109, J1.110, J1.111, J1.112, TP3.1, U1.8 (R8.1), U2.8 (R8.1), U3.8 (R8.1), U4.8 (R8.1), U5.8 (GND), U6.7 (GND), U7.1 (GND), U8.7 (GND), U9.7 (GND), U10.7 (GND), U11.8 (GND), U12.7 (GND), U13.7 (GND), U14.8 (GND), U14.12 (A3), U15.8 (GND), U16.8 (GND), U17.8 (GND), U18.1 (GND), U19.1 (GND), U20.12 (GND), U20.18 (PGM), U21.12 (GND), U21.18 (~CE), U22.12 (GND), U22.18 (PGM), U23.8 (GND), U24.8 (GND), U25.1 (VSS), U25.21 (GND)
INTRO in: J1.45, U18.10 (PA2)
INTRO out: J1.117, U12.10
MIKE SW.: J1.42, U19.8 (PA0)
NEXT in: J1.49, U18.13 (PA5)
NEXT out: J1.113, U12.4
unnamed: C2.1, CR1.1 (K), CR2.2 (A), R3.2, U25.37 (00), Y1.1
unnamed: C3.1, CR3.2 (A), R4.2, R5.2, U6.3
unnamed: CR4.2 (A), RP2.1 (R1.1), U25.33 (D0), XU1.1 (R1.1)
unnamed: CR4.1 (K), CR5.1 (K), CR6.1 (K), TP6.1
unnamed: CR5.2 (A), RP2.3 (R3.1), U25.31 (D2), XU1.3 (R3.1)
unnamed: CR6.2 (A), RP2.5 (R5.1), U25.29 (D4), XU1.5 (R5.1)
unnamed: DS1.2 (A), RP1.9 (R8.2)
unnamed: DS1.1 (K), U8.12
unnamed: DS2.2 (A), RP1.10 (R7.2)
unnamed: DS2.1 (K), U8.10
unnamed: DS3.2 (A), RP1.11 (R6.2)
unnamed: DS3.1 (K), U8.8
unnamed: DS4.2 (A), RP1.12 (R5.2)
unnamed: DS4.1 (K), U13.12
unnamed: DS5.2 (A), RP1.13 (R4.2)
unnamed: DS5.1 (K), U13.2
unnamed: DS6.2 (A), RP1.14 (R3.2)
unnamed: DS6.1 (K), U8.6
unnamed: DS7.2 (A), RP1.15 (R2.2)
unnamed: DS7.1 (K), U8.4
unnamed: DS8.2 (A), RP1.16 (R1.2)
unnamed: DS8.1 (K), U8.2
unnamed: R3.1, U6.9, U6.10, Y1.2
unnamed: RP2.2 (R2.1), U25.32 (D1), XU1.2 (R2.1)
unnamed: RP2.4 (R4.1), U25.30 (D3), XU1.4 (R4.1)
unnamed: RP2.6 (R6.1), U25.28 (D5), XU1.6 (R6.1)
unnamed: RP2.7 (R7.1), U25.27 (D6), XU1.7 (R7.1)
unnamed: RP2.8 (R8.1), U25.26 (D7), XU1.8 (R8.1)
unnamed: U6.4, U6.5
unnamed: U9.6, U9.9
unnamed: U10.3, U11.13 (A2)
unnamed: U10.11, U11.12 (A3)
unnamed: U14.1 (0), U15.12 (A3), U16.1 (~CS), U17.1 (~CS)
unnamed: U9.8, U16.15 (IN/~OUT), U17.15 (IN/~OUT)
unnamed: R8.2, TP7.1, U18.38 (CS1)
unnamed: U13.3, U18.24 (PB0)
unnamed: U12.13, U18.23 (PB1)
unnamed: U12.11, U18.22 (PB2)
unnamed: U12.9, U18.21 (PB3)
unnamed: U12.5, U18.19 (PB4)
unnamed: U12.3, U18.18 (PB5)
unnamed: U12.1, U18.17 (PB6)
unnamed: U13.5, U18.16 (PB7)
unnamed: U9.5, U9.11, U18.37 (~CS2)
unnamed: R9.2, TP8.1, U19.38 (CS1)
unnamed: U13.9, U19.9 (PA1)
unnamed: U8.13, U19.24 (PB0)
unnamed: U8.11, U19.23 (PB1)
unnamed: U8.9, U19.22 (PB2)
unnamed: U13.13, U19.21 (PB3)
unnamed: U13.1, U19.19 (PB4)
unnamed: U8.5, U19.18 (PB5)
unnamed: U8.3, U19.17 (PB6)
unnamed: U8.1, U19.16 (PB7)
unnamed: U9.3, U9.4, U19.37 (~CS2)
unnamed: U5.1 (OEa), U5.15 (OEb), U6.2, U23.1 (OEa), U23.15 (OEb), U24.1 (OEa), U24.15 (OEb)
unnamed: C2.2, U6.11, U25.39 (02)
unnamed: R7.2, U25.6 (~NMI), U25.38 (SO)
PHI2: J1.68, U6.8, U18.39 (02), U19.39 (02)
PROG in: C1.1, J1.48, U18.15 (PA7)
PROG out: J1.114, U13.6
RDY: J1.95, R1.2, U25.2 (RDY)
RESET out: J1.59, U13.8
R/~W: J1.66, U5.13 (O6b), U9.10, U18.35 (R/~W), U19.35 (R/~W)
SKIP in: J1.51, U18.14 (PA6)
SKIP out: J1.120, U12.2
SPEC in: J1.46, U18.11 (PA3)
SPEC out: J1.121, U12.8
UART: J1.77, U15.3 (2)
XPRT: J1.17, U15.7 (6)
cpu R/~W: U5.14 (I6), U25.34 (R/~W)
/CARDS: U10.2, U10.13, U15.2 (1)
/CS 2732: R10.2, U13.10, U21.20 (~OE/VPP)
/CS U20: U14.9 (7), U20.20 (~CS)
/CS U22: U14.6 (5), U22.20 (~CS)
/HOLD in: J1.34, R2.2, U6.1
/IRQ: R6.2, TP9.1, U18.25 (~IRQ), U19.25 (~IRQ), U25.4 (~IRQ), W1.1
/IRQ out: J1.36, W1.2
/RAM: U9.12, U15.1 (0), U18.36 (/RS)
/RESET: J1.67, U6.6, U18.34 (~RESET), U19.34 (~RESET), U25.40 (~RESET)
/RESET in: J1.50, R5.1
/STACK: U9.1, U15.4 (3), U19.36 (/RS)
/U18: U9.13, U15.5 (4)
/U19: U9.2, U15.6 (5)

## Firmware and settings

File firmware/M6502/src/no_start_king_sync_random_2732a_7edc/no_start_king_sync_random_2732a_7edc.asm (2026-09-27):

        .area   region1 (ABS)

TIMER_1MS_A     = 0x0050    ; 1ms timer
TIMER_1MS_B     = 0x0051    ; 1ms timer
TIMER_1MS_C     = 0x0052    ; 1ms timer
TIMER_1MS_R     = 0x0053    ; 1ms timer, autoload to 100
TIMER_100MS_A   = 0x0054    ; 0.1s timer
TIMER_100MS_B   = 0x0055    ; 0.1s timer
TIMER_100MS_R   = 0x0056    ; 0.1s timer, autoload to 100
TIMER_10S       = 0x0057    ; 10s timer
ZEROCROSS_CTR   = 0x0058    ; zero crossing counter
TRACK_CTR       = 0x0059    ; track counter

TAPE_BYTE       = 0x005B    ; storage for incoming serial byte (& 0x7F)
SOL_MASK        = 0x005C    ; bitmask for solenoids
CURR_CHANNEL    = 0x005D    ; current channel serial byte

AGC_LEVEL       = 0x005F    ; agc mic level
AGC_ACCUM       = 0x0060    ; agc mic level accumulator
AGC_SAMPLES     = 0x0061    ; agc mic sample counter
AGC_GAIN        = 0x0062    ; agc calculated gain value
CURR_PORT       = 0x0063    ; current channel port address
TIMER_100MS_C   = 0x0064    ; 0.1s timer
KTABLE_OFFS     = 0x0065    ; offset into King table
KTABLE_SEL      = 0x0066    ; select King table
UART_RBYTE      = 0x0067    ; UART routine recv byte (0 or 1)
UART_SBYTE      = 0x0068    ; UART routine send byte (0 or 1)
UART_ADDR       = 0x0069    ; Address of UART send table (2 bytes)

        .include "../../include/ptt6502.def"

        .org    0x1000

;
;       IRQ handler
;
IRQ:
        pha
        lda     U18_edge_detect_control_DI_pos          ; clear PA7 flag
        lda     U19_edge_detect_control_DI_pos          ; clear PA7 flag
        lda     #0x7D                                   ; expire every 125*8=1000us=1ms
        sta     U18_1D                                  ; div by 8, enable interrupt
        lda     TIMER_1MS_A                             ; 1ms timer
        beq     $50
        dec     TIMER_1MS_A
$50:
        lda     TIMER_1MS_B                             ; 1ms timer
        beq     $51
        dec     TIMER_1MS_B
$51:
        lda     TIMER_1MS_C                             ; 1ms timer
        beq     $52
        dec     TIMER_1MS_C
$52:
        dec     TIMER_1MS_R
        bne     $56
        lda     #0x64
        sta     TIMER_1MS_R
        lda     TIMER_100MS_A
        beq     $53
        dec     TIMER_100MS_A
$53:
        lda     TIMER_100MS_C
        beq     $54
        dec     TIMER_100MS_C
$54:
        lda     TIMER_100MS_B
        beq     $55
        dec     TIMER_100MS_B
$55:
        dec     TIMER_100MS_R
        bne     $56
        lda     #0x64
        sta     TIMER_100MS_R
        lda     TIMER_10S
        beq     $56
        dec     TIMER_10S
$56:
        pla
        rti
;
;       Main Program Start
;
RESET:
        cld                                             ; No decimal mode
        sei                                             ; Interrupts are not used
        ldx     #0xF0                                   ; Stack is at 0x01F0
        txs
        lda     #0x00                                   ; Clear RAM
        ldx     #0x10                                   ; from 0x0010 to 0x007F
ZERORAM:
        sta     0x00,x
        inx
        cpx     #0x80
        bne     ZERORAM
        lda     #0x00
        sta     transport_control_reg_a                 ; Clear transport control A, select DDRA
        sta     transport_periph$ddr_reg_a              ; UART data inputs
        sta     audio_control_reg_a                     ; Clear audio control A, select DDRA
        sta     audio_periph$ddr_reg_a                  ; Comparator inputs
        sta     audio_control_reg_b                     ; Clear audio control B
        sta     U18_edge_detect_control_DI_pos          ; Detect PROG button release
        sta     transport_control_reg_b                 ; Clear transport control B, select DDRB
        sta     U18_06                                  ; ???
        sta     U19_06                                  ; ???
        sta     U18_DDRA                                ; Buttons are inputs
        lda     #0x02
        sta     U19_DDRA                                ; AGC and MIKESW are inputs, RESET Light output
        lda     #0xFF
        sta     audio_periph$ddr_reg_b                  ; DAC08 outputs
        sta     U18_DDRB                                ; Button lights are outputs
        sta     U19_DDRB                                ; CPU card lights are outputs
        lda     #0xFC
        sta     transport_periph$ddr_reg_b              ; transport control, chip control are outputs, PB1 & PB0 inputs
        lda     #0x2E
        sta     transport_control_reg_a                 ; transport CA2 is Read strobe (~DDR), set IRQA bit on ~DR low to high 
        sta     transport_control_reg_b                 ; transport CB2 is Write strobe (~THRL), set IRQB bit on CB1 low to high
        lda     #0x3C
        sta     audio_control_reg_a                     ; CA2 High - Disable BG Audio
        sta     audio_control_reg_b                     ; CB2 high - Disable Tape Audio
        cli
        sta     U18_1C
        lda     #0x64
        sta     TIMER_1MS_R                             ; 100 - init 1 msec master counter
        lda     #0x18
        sta     TIMER_10S                               ; Init a 4 minute timer
        lda     #0x64
        sta     TIMER_100MS_R                           ; 100 - init 0.1 sec master counter
        lda     #0x0A                                   ; 10
        sta     AGC_GAIN                                ; Set initial AGC gain value
        lda     #0x09
        sta     UART_02                                 ; ???
        lda     #TAPEMODE_STOP
        jsr     TAPECMD                                 ; STOP tape
        lda     #0x28                                   ; this will count 4 seconds
        sta     TIMER_100MS_A
        lda     #0x64                                   ; reset master timer
        sta     TIMER_1MS_R
$1:
        lda     TIMER_100MS_A                           ; do not much for 4 seconds
        bne     $1
        jsr     INITBRDS
REWIND:
        lda     #0xFA
        sta     TIMER_100MS_C
        lda     #0x00
        sta     KTABLE_OFFS
        sta     KTABLE_SEL
        lda     #0x30
        lda     #TAPEMODE_REWIND
        jsr     TAPECMD                                 ; REWIND tape
$22:
        lda     #0x00
        sta     ZEROCROSS_CTR                           ; counter to zero
$3:
        lda     transport_periph$ddr_reg_b
        lda     #0x0A
        sta     TIMER_1MS_A                             ; set a 10ms timer
        inc     ZEROCROSS_CTR                           ; count transitions
        lda     ZEROCROSS_CTR
        cmp     #0x64
        bcs     FINDTRK                                 ; happened 100 times, tape is at the beginning, jump ahead
$4:
        jsr     KUPDATE
        lda     TIMER_1MS_A
        beq     $22
        lda     transport_control_reg_b
        bpl     $4
        jmp     $3
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

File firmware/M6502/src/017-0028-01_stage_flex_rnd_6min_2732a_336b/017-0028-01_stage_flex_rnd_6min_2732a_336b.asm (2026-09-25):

        .area   region1 (ABS)

        .include "../../include/ptt6502.def"

        .org    0x1000

L1000:
        pha
        lda     U18_edge_detect_control_DI_pos
        lda     U19_edge_detect_control_DI_pos
        lda     #0x7D
        sta     U18_1D
        lda     0x4B
        beq     L1012
        dec     0x4B


L1012:
        lda     0x4C
        beq     L1018
        dec     0x4C


L1018:
        lda     0x4D
        beq     L101E
        dec     0x4D


L101E:
        dec     0x4E
        bne     L1064
        lda     #0x64
        sta     0x4E
        lda     0x4F
        beq     L102C
        dec     0x4F


L102C:
        lda     0x50
        beq     L1032
        dec     0x50


L1032:
        lda     0x51
        beq     L1038
        dec     0x51


L1038:
        lda     0x3E
        beq     L103E
        dec     0x3E


L103E:
        lda     0x3F
        beq     L1044
        dec     0x3F


L1044:
        lda     0x40
        beq     L104A
        dec     0x40


L104A:
        lda     0x41
        beq     L1050
        dec     0x41


L1050:
        lda     0x42
        beq     L1056
        dec     0x42


L1056:
        dec     0x52
        bne     L1064
        lda     #0x64
        sta     0x52
        lda     0x53
        beq     L1064
        dec     0x53


L1064:
        pla
        rti


L1066:
        cld
        sei
        ldx     #0xF0
        txs
        lda     #0x00
        ldx     #0x10


L106F:
        sta     0x00,x
        inx
        cpx     #0x80
        bne     L106F
        lda     #0x00
        sta     transport_control_reg_a
        sta     U18_PORTB
        sta     audio_control_reg_a
        sta     audio_control_reg_b
        sta     U18_edge_detect_control_DI_pos
        sta     U19_edge_detect_control_DI_pos
        sta     U18_06
        sta     U19_06
        sta     transport_control_reg_b
        sta     U18_DDRA
        lda     #0x02
        sta     U19_DDRA
        sta     U19_PORTA
        lda     #0xFF
        sta     audio_periph$ddr_reg_b
        sta     U18_DDRB
        sta     U19_DDRB
        lda     #0xFC
        sta     transport_periph$ddr_reg_b
        lda     #0x2E
        sta     transport_control_reg_a
        sta     transport_control_reg_b
        lda     #0x3C
        sta     audio_control_reg_b
        sta     audio_control_reg_a
        lda     #0x10
        sta     audio_periph$ddr_reg_b
        sta     U19_PORTB
        lda     #0x00
        sta     0x5E
        lda     #0x64
        sta     0x4E
        cli
        sta     U18_1C
        jsr     L18A0
        jsr     L163D
        lda     #0x02
        sta     U19_PORTA
        lda     #0x10
        jsr     L1530
        lda     #0x28
        sta     0x4F


L10E6:
        jsr     L18DD
        lda     0x4F
        bne     L10E6
        jsr     L163D
        jsr     L184E
        lda     U18_PORTA
        eor     #0xFF
        cmp     #0x10
        bne     L110C
        lda     #0xFF
        sta     0x98
        sta     0x9A
        sta     0x9C
        sta     0x9E
        sta     U18_PORTB


L1109:
        jmp     L1109


L110C:
        lda     #0x40
        jsr     L1530
        lda     0x55
        sta     U19_PORTB


L1116:
        lda     #0x00
        sta     0x59


L111A:
        lda     transport_periph$ddr_reg_b
        lda     #0x0A
        sta     0x4B
        inc     0x59
        lda     0x59
        cmp     #0x64
        bcs     L1138


L1129:
        jsr     L18DD
        lda     0x4B
        beq     L1116
        lda     transport_control_reg_b
        bpl     L1129
        jmp     L111A


L1138:
        lda     #0x20
        jsr     L1530
        lda     #0x19
        sta     0x4F


L1141:
        jsr     L18DD
        lda     0x4F
        bne     L1141
        lda     #0x00
        sta     0x55
        lda     #0x01
        sta     0x56
        sta     0x57
        jsr     L146B
        lda     #0x80
        jsr     L1530
        jsr     L14D0
        lda     #0x96
        sta     0x4F
        lda     #0x80
        jsr     L1530
        jsr     L1530


L1169:
        jsr     L11E2
        cmp     #0x24
        bne     L1169


L1170:
        jsr     L11E2
        cmp     #0x24
        beq     L1170
        and     #0x3F
        cmp     0x56
        beq     L1184
        jmp     L1066
        lda     #0x00
        sta     0x49


L1184:
        jsr     L11E2
        cmp     #0x28
        bne     L1184
        jsr     L11E2
        cmp     #0x47
        bcc     L11BD
        cmp     #0x5A
        bcs     L11BD
        and     #0x1F
        ldx     #0x00
        ldy     #0x00


L119C:
        sta     0x70,x
        inx
        jsr     L11E2
        cmp     X11DA,y
        beq     L119C
        iny
        cmp     X11DA,y
        bne     L11BD
        cpy     #0x07
        bne     L119C
        dex
        cpx     0x70
        bne     L11BD
        lda     #0x00
        sta     0x49
        jmp     L1202


L11BD:
        lda     0x49
        beq     L11D3


L11C1:
        lda     #0xFF
        sta     0x49
        sta     U18_PORTB
        sta     U19_PORTB
        lda     #0x10
        jsr     L1530
        jmp     L11C1


L11D3:
        lda     #0x80
        sta     0x49
        jmp     L1184


X11DA:
        .byte   0x44,0x52,0x42,0x43,0x53,0x49,0x52,0x29

L11E2:
        lda     0x4F
        beq     L11F1
        lda     transport_control_reg_a
        bpl     L11E2
        lda     transport_periph$ddr_reg_a
        and     #0x7F
        rts


L11F1:
        lda     0x49
        beq     L11F8
        jmp     L11C1


L11F8:
        lda     #0x0F
        sta     0x49
        lda     #0x02
        sta     0x57
        pla
        pla


L1202:
        jsr     L18A0
        lda     #0x02
        sta     0x56
        jsr     L146B
        lda     #0x00
        sta     U19_PORTA
        lda     #0x00
        sta     0x63


L1215:
        lda     #0x24
        sta     0x53


L1219:
        lda     #0x0A
        sta     0x4F


L121D:
        jsr     L18DD
        lda     0x63
        bmi     L1227
        jsr     L15D7


L1227:
        lda     0x6B
        bmi     L1272
        bne     L123E
        lda     #0x64
        sta     0x50
        lda     #0x80
        jsr     L1530
        lda     #0x03
        sta     0x6B
        lda     #0xA0
        sta     0x4C


L123E:
        lda     0x6B
        ror
        bcc     L124E
        lda     0x50
        bne     L124E
        lda     #0x02
        sta     0x6B
        jmp     L1265


L124E:
        lda     transport_periph$ddr_reg_b
        ror
        bcs     L1258
        lda     #0xA0
        sta     0x4C


L1258:
        lda     0x4C
        bne     L126D
        lda     #0x10
        jsr     L1530
        lda     #0x80
        sta     0x6B


L1265:
        lda     #0x80
        and     U18_PORTB
        sta     U18_PORTB


L126D:
        lda     0x6B
        ror
        bcs     L121D
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

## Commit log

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2024-03-03 started audio card rev a
    [Audio board rev.a.kicad_pcb, Audio board rev.a.kicad_sch]
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2024-03-06 audio board rev a agc circuit probably complete
    [Audio board rev.a.kicad_sch]
2024-03-06 sorted out U11 and some of the card edge
    [Audio board rev.a.kicad_sch]
2024-03-06 working on U9 section
    [Audio board rev.a.kicad_sch]
2024-03-06 half of u9 done
    [Audio board rev.a.kicad_sch]
2024-03-06 finished initial layout and added backplane notes from san jose trip
    [Audio board rev.a.kicad_sch, backplane.kicad_sch]
2024-03-06 fixed resistor value, moved bgaudio amp to logical location
    [Audio board rev.a.kicad_sch]
2024-03-06 board outline done, picking footprints
    [Audio board rev.a.kicad_pcb, Audio board rev.a.kicad_sch]
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2024-03-07 U7/U9 area laid out, best guess on 0.025" grid for silk, 0.05" grid for parts
    [Audio board rev.a.kicad_pcb, Audio board rev.a.kicad_sch]
2024-03-07 initial placement of components done
    [Audio board rev.a.kicad_pcb]
2024-03-08 most of layout done, fixed some bugs
    [Audio board rev.a.kicad_pcb, Audio board rev.a.kicad_sch]
2024-03-08 front copper fill done
    [Audio board rev.a.kicad_pcb]
2024-03-08 layout done minus logo
    [Audio board rev.a.kicad_pcb]
2024-03-09 tweaked backplane wording to reflect schematic date
    [backplane.kicad_sch]
2024-03-09 initial rev c layout completed
    [Audio board rev.c.kicad_pcb, Audio board rev.c.kicad_sch]
2024-03-09 layout tweaks to reva
    [Audio board rev.a.kicad_pcb]
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2024-03-09 tweaked copper fills on revc
    [Audio board rev.c.kicad_pcb, Audio board rev.c.kicad_sch]
2024-03-09 copper layer on reva
    [Audio board rev.a.kicad_pcb]
2024-03-09 updated some labels on backplane from audio cards
    [backplane.kicad_sch]
2024-03-09 labeled pins 64 and 65
    [Audio board rev.a.kicad_sch, Audio board rev.c.kicad_sch]
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2024-03-17 revised hole position in audio cards based on character card
    [Audio board rev.a.kicad_pcb, Audio board rev.c.kicad_pcb]
2024-03-17 initial character card rev a parts and partial layout
    [Character board rev.a.kicad_pcb, Character board rev.a.kicad_sch]
2024-03-17 character card rev a done
    [Character board rev.a.kicad_pcb, Character board rev.a.kicad_sch]
2024-03-17 revised copper layer character card rev a
    [Character board rev.a.kicad_pcb]
2024-03-17 revised schematic to more match paper one
    [Character board rev.a.kicad_sch]
2024-03-17 character card rev b done
    [Character board rev.b.kicad_pcb, Character board rev.b.kicad_sch]
2024-03-17 revised all net names to reflect new information about 4 channel audio system
    [Audio board rev.a.kicad_sch, Audio board rev.c.kicad_sch, Character board rev.a.kicad_sch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]
2024-03-17 renaming a lot of files to be more explicit
    [Character board 0004 rev.a.kicad_pcb, Character board 0004 rev.a.kicad_sch, Character board 0004 rev.b.kicad_pcb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]
2024-03-17 updated boards to have correct logos
    [Audio board rev.a.kicad_pcb, Audio board rev.c.kicad_pcb, Character board 0004 rev.a.kicad_pcb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]
2024-03-18 completed 0034 rev a
    [Character board 0034 rev.a.kicad_pcb, Character board 0034 rev.a.kicad_sch]
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2024-03-18 starting the first rev character driver compatible with the av switcher
    [Character board 0034 rev.d.kicad_pcb, Character board 0034 rev.d.kicad_sch]
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2024-03-18 revised LED spacing rev a
    [Character board 0004 rev.a.kicad_pcb]
2024-03-18 revised 0034 rev a led spacing and fuse length
    [Character board 0034 rev.a.kicad_pcb]
2024-03-18 rev d layout done
    [Character board 0034 rev.d.kicad_pcb, Character board 0034 rev.d.kicad_sch]
2024-03-18 renamed files and started the light card
    [Audio board 0003 rev.c.kicad_pcb, Audio board 0003 rev.c.kicad_sch, Audio board 0033 rev.a.kicad_pcb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]
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2024-03-19 almost done with the old light driver
    [Light board 0021 rev.0.kicad_pcb, Light board 0021 rev.0.kicad_sch]
2024-03-19 finish light board rev.a, rename files, add renders and schematics, move pictures
    [Audio board 0003 rev.c.kicad_sch, Audio board 0033 rev.a.kicad_sch, Character board 0034 rev.a.kicad_sch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]
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2024-03-19 revised some test points per pictures of real boards
    [Transpoart board 0020 rev.1982.kicad_sch]
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2024-03-23 Fix spelling errors with Transport
    [CPU board 0001 rev.a.kicad_sch, Transport board 0020 rev.1982.kicad_pcb, Transport board 0020 rev.1982.kicad_sch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]
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2024-03-26 checked Rev.c cpu board and tweaked copper on a and b
    [CPU board 0001 rev.b.kicad_pcb, CPU board 0001 rev.b.kicad_sch, CPU board 0001 rev.c.kicad_pcb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]
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2024-04-30 revisions from real life boards
    tip130a is actually tip30a, widened holes for crystal, widened holes for big power resistor, fixed cpu board LED resistors
    [CPU board 0001 rev.a.kicad_pcb, CPU board 0001 rev.a.kicad_sch, CPU board 0001 rev.b.kicad_pcb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]
2024-04-30 revised value of resistor to 1k per board
    [Character board 0034 rev.d.kicad_pcb, Character board 0034 rev.d.kicad_sch]
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2024-05-20 revised PCBs based on Jen's boards, added rev.c
    [Character board 0004 rev.b.kicad_pcb, Character board 0004 rev.b.kicad_sch, Character board 0034 rev.c.kicad_pcb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]
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2024-05-23 added button board initial schematic (no custom buttons yet)
    [Button board 007 rev.f.kicad_pcb, Button board 007 rev.f.kicad_sch]
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2024-05-26 Regularize RAM variables. Add missing def file.
    [dolli_c.asm, halfchuck.asm, unknown2.asm]
2024-05-30 Disassembled new code from Cyberstar1.7 more correctly. Added new labels for all Branch addresses consistently
    [cyberstar16.asm, cyberstar17.asm]
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2024-07-28 fixed 50 pin ribbon, added 3d models
    [50 pin ribbon adapter.kicad_pcb, 50 pin ribbon adapter.kicad_sch, CEC ejector.SLDPRT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]
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2024-08-19 fixed rev.d pull up on CS and added render and schematic
    [CPU board 0001 rev.d.kicad_pcb, CPU board 0001 rev.d.kicad_sch]
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2024-08-30 added LCD mount adapter and new version of LCD board for modern LCDs
    [CEC LCD Adapter.SLDPRT, CEC LCD Adapter.STL, LCD board modified.kicad_pcb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]
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2025-04-18 added audio board schematics and de9 board fab files
    [Character board DE9 adapter.kicad_pcb, Character board DE9 adapter.kicad_sch, Solenoid board DE9 adapter.kicad_pcb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]
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2025-11-06 added images with which to revise card designs (from Boris)
    [Transport board 0020 rev.b.kicad_pcb]
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2026-01-26 fixed typo
    [LCD board modified.kicad_pcb]
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2026-03-12 Add a couple missing symbols
    [017-0028-01_stage_flex_rnd_6min_2732a_336b.asm]
2026-03-14 Fix issue with serial number
    [017-0150-01_kingbeagles_sync_799d.asm]
